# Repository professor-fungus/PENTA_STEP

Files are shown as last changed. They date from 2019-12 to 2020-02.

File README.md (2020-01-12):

# PENTA_STEP

I hate tracking down EMI through jumpers.

This is my attempt to create a stepper driver board that can be loaded with up to 5 stepper drives.

If one fails, it will require soldering rework; this may not be optimal for those without SMD rework tools.

The drives utilize Trinamic TMC5160's, based on the schematic for the TMC5160-BOB.

Why five drives? 
* 3 axes and 2 extruders for 3D printing.
* 3 cartesian axes and 2 orthogonal axes for milling.
* 5 axis robots.
* Too little space for 4 drives on a 100mmx100mm board from JLCPCB, so go big or go home.

If less than 5 axes are desired, less can be populated (although this wouldn't save much).

Target is a 4-layer board currently.

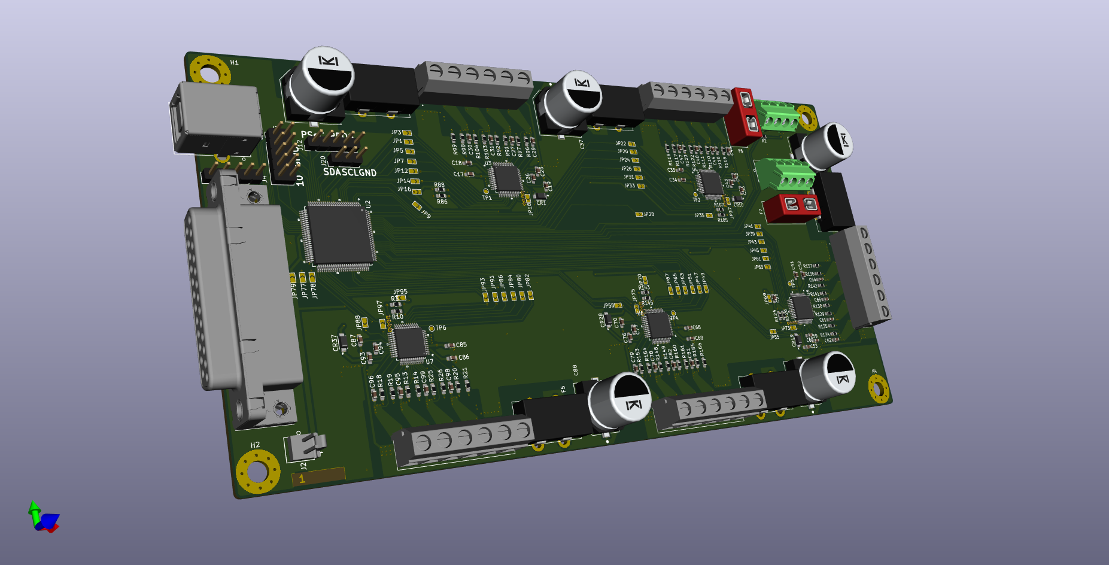
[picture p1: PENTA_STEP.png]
Test Image 1


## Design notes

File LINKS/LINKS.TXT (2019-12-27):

Dual MOSFET footprint info:
https://assets.nexperia.com/documents/outline-drawing/SOT1205.pdf

minimal ATTINY841
http://elecrab.com/archives/826

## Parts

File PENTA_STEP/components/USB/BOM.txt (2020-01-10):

3DX_CUI_DEVICES_Supplier: CUI Devices
3DX_CUI_DEVICES_Description: 3 µin Plating Thickness, White Insulator, USB Receptacle
3DX_CUI_DEVICES_Model Number: UJ2-BH-W1-TH

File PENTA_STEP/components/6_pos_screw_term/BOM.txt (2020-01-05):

3DX_CUI_DEVICES_Supplier: CUI Devices
3DX_CUI_DEVICES_Part Number: TB002-500-06BE
3DX_CUI_DEVICES_Description: 2~24 Poles, Screw Type, Horizontal, 5.0 Pitch, 22-12 (AWG), Terminal Block Connector

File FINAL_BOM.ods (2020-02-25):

REFDES |  |  |  |  | DPN |  | QTY
> C8-C11, C13-C16, C23-C25, C33, C40-C42, C50, C57-C59, C67, C74-C76, C84, C91-C93 | 100n | Capacitor_SMD:C_0603_1608Metric_Pad1.05x0.95mm_HandSolder |  | CL10B104KC8NNNC,1276-6807-1-ND | 478-10047-1-ND | 06031C104KAT2A | 27
> C3, C4, C6, C12 | 1u | Capacitor_SMD:C_0603_1608Metric_Pad1.05x0.95mm_HandSolder |  | CC0603KRX7R7BB105,311-1446-1-ND | 1276-6524-1-ND | CL10B105MO8NNWC | 4
> C17, C18, C34, C35, C51, C52, C68, C69, C85, C86 | 2u2 | Capacitor_SMD:C_0603_1608Metric_Pad1.05x0.95mm_HandSolder | ~ | EMK107BJ225KA-T,587-1430-1-ND | 1276-1040-1-ND | CL10A225KO8NNNC | 10
> C19, C29, C32, C36, C46, C49, C53, C63, C66, C70, C80, C83, C87, C97, C100 | 470n | Capacitor_SMD:C_0603_1608Metric_Pad1.05x0.95mm_HandSolder | ~ | CL10A474KP8NNNC,1276-1898-1-ND | 732-7905-1-ND | 885012106008 | 15
> C20, C37, C54, C71, C88 | 150u 80V | CUSTOM_FP:CAPAE1350X1400N_EEVFK1J151Q | ~ | EMHS800ARA181MKE0S,565-5083-1-ND | PCE3494CT-ND | EEV-FK1K151Q | 5
> C21, C22, C38, C39, C55, C56, C72, C73, C89, C90 | 10u | Capacitor_SMD:C_1210_3225Metric_Pad1.42x2.65mm_HandSolder |  | C3225X7R1N106K250AC,445-C3225X7R1N106K250ACCT-ND | 445-C3225X7R1N106M250ACCT-ND | C3225X7R1N106M250AC | 10
> C26, C43, C60, C77, C94 | 22n | Capacitor_SMD:C_0603_1608Metric_Pad1.05x0.95mm_HandSolder |  | C0603C223K1RACTU,399-3476-1-ND | 1276-1104-1-ND | CL10B223KB8NNNC | 5
> C27, C28, C30, C31, C44, C45, C47, C48, C61, C62, C64, C65, C78, C79, C81, C82, C95, C96, C98, C99 | 220n | Capacitor_SMD:C_0603_1608Metric_Pad1.05x0.95mm_HandSolder | ~ | CC0603ZRY5V9BB224,311-1830-1-ND | 1276-2367-1-ND | CL10F224ZB8NNNC | 20
> CR1, CR10, CR19, CR28, CR37 | PMEG6010CEGWX | CUSTOM_FP:PMEG6010CEGWX |  |  | S310FACT-ND | S310FA | 5
> F1-F5 | BLADE_Fuse | CUSTOM_FP:keystone_3549_2_fuseholder_THT | ~ |  | 36-3549-2-ND | 3549-2 | 5
> F6, F7 | BLADE_Fuse | CUSTOM_FP:keystone_3568_10_fuseholder_THT | ~ |  | 36-3568-10-ND | 3568-10 | 2
> H1-H4 | MountingHole_Pad | MountingHole:MountingHole_4.5mm_Pad_Via | ~ |  |  |  | 4
J1 | DB25_Female_LCNC | CUSTOM_FP:DSUB-25_Female_Horizontal_P2.77x2.84mm_EdgePinOffset7.70mm_Housed_MountingHolesOffset9.12mm | ~ |  | 2057-DB25-SL-25-ND | DB25-SL-25 | 1
J2 | MTA-100 | CUSTOM_FP:640456-2 | ~ |  | A1921-ND | 640456-2 | 1
J3 | USB_B | CUSTOM_FP:CUI_UJ2-BH-W1-TH | ~ |  | 102-5887-ND | UJ2-BH-W1-TH | 1
J4 | SPARE_IN | Connector_PinHeader_2.54mm:PinHeader_1x05_P2.54mm_Vertical | ~ |  |  |  | 1
J7 | CYP_GPIO | Connector_PinHeader_2.54mm:PinHeader_2x05_P2.54mm_Vertical | ~ |  |  |  | 1
> J5, J10, J11, J16, J17 | ENC_HEADER | Connector_PinHeader_1.00mm:PinHeader_1x04_P1.00mm_Vertical | ~ |  | HDR100MET40M-G-RA-TH-ND | HDR100MET40M-G-RA-TH | 5
J12 | PSoC_PROG | Connector_PinHeader_2.54mm:PinHeader_1x05_P2.54mm_Vertical | ~ |  |  |  | 1
J13 | PWR_SW_CH1 | CUSTOM_FP:1776275-4 | ~ |  | 277-1781-ND | 1988972 | 1
> J9, J14, J15, J18, J19 | SCREW TERM | CUSTOM_FP:CUI_TB002-500-06BE | ~ |  | 102-6149-ND | TB002-500-06BE | 5
J20 | CYP_I2C | Connector_PinHeader_2.54mm:PinHeader_1x03_P2.54mm_Vertical | ~ |  |  |  | 1
J21 | PWR_SW_CH2 | CUSTOM_FP:1776275-4 | ~ |  | 277-1781-ND | 1988972 | 1
> JP1, JP3, JP5, JP7, JP9, JP11-JP16, JP18-JP20, JP22, JP24, JP26, JP28, JP30-JP35, JP37-JP39, JP41, JP43, JP45, JP47, JP49, JP51, JP53, JP55, JP57, JP58, JP60-JP70, JP73-JP80, JP82, JP84, JP86, JP88, JP90-JP95, JP97, JP98 | SolderJumper_2_Open | CUSTOM_FP:small_triangle_jumper | ~ |  |  |  | 68
> Q1-Q20 | BUK9K45-100E,115 | CUSTOM_FP:TRANS_BUK7K12-60EX | https://assets.nexperia.com/documents/data-sheet/BUK9K45-100E.pdf |  | 1727-7272-1-ND | BUK9K45-100E,115 | 20
> Q2, Q4, Q6, Q8, Q10, Q12, Q14, Q16, Q18, Q20 | BUK9K45-100E,115 | CUSTOM:TRANS_BUK7K12-60EX | https://assets.nexperia.com/documents/data-sheet/BUK9K45-100E.pdf |  | 1727-7272-1-ND | BUK9K45-100E,115 | 10
Q21 | AON7804 | CUSTOM_FP:DFN3X3_AON7804 |  |  | 785-1586-1-ND | AON7804 | 1
> R1, R2, R12, R90, R109, R128, R147 | 2R2 | Resistor_SMD:R_0603_1608Metric_Pad1.05x0.95mm_HandSolder | ~ | RMCF0603FT2R20,RMCF0603FT2R20CT-ND | 311-2.2HRCT-ND | RC0603FR-072R2L | 7
> R5, R6, R13, R14, R18-R21, R25, R26, R91, R92, R96-R99, R103, R104, R110, R111, R115-R118, R122, R123, R129, R130, R134-R137, R141, R142, R148, R149, R153-R156, R160, R161 | 22R | Resistor_SMD:R_0603_1608Metric_Pad1.05x0.95mm_HandSolder | ~ | CRGCQ0603J22R,A130081CT-ND | P22.0HCT-ND | ERJ-3EKF22R0V | 42
> R4, R10, R87, R88, R106, R107, R125, R126, R144, R145 | DNP | Resistor_SMD:R_0603_1608Metric_Pad1.05x0.95mm_HandSolder | ~ | ERJ-3GEY0R00V,P0.0GCT-ND | 311-0.0GRCT-ND | RC0603JR-070RL | 10
> R3, R11, R86, R89, R105, R108, R124, R127, R143, R146 | 0R | Resistor_SMD:R_0603_1608Metric_Pad1.05x0.95mm_HandSolder | ~ | ERJ-3GEY0R00V,P0.0GCT-ND | 311-0.0GRCT-ND | RC0603JR-070RL | 10
> R15, R16, R22, R23, R93, R94, R100, R101, R112, R113, R119, R120, R131, R132, R138, R139, R150, R151, R157, R158 | 47R | Resistor_SMD:R_0603_1608Metric_Pad1.05x0.95mm_HandSolder | ~ | RMCF0603FT47R0,RMCF0603FT47R0CT-ND | A129672CT-ND | CRGCQ0603F47R | 20
> R17, R24, R95, R102, R114, R121, R133, R140, R152, R159 | 0R022 | CUSTOM_FP:WSH2818R0500FEA | ~ |  | 541-10297-1-ND | WSHM2818R0220FEA | 10
> R162, R163 | 10k | Resistor_SMD:R_0603_1608Metric_Pad1.05x0.95mm_HandSolder | ~ | ERJ-3GEYJ103V,P10KGCT-ND | 311-10KGRCT-ND | RC0603JR-0710KL | 2
> TP1-TP4, TP6 | CLK16 | TestPoint:TestPoint_Pad_D1.0mm | ~ |  |  |  | 5
TP5 | PAR_SPARE | TestPoint:TestPoint_Pad_D1.0mm | ~ |  |  |  | 1
U2 | CY8C5468AXI-LP106 | CUSTOM_FP:CY8C5468AXI-LP106 |  |  | 2015-CY8C5468AXI-LP106-ND | CY8C5468AXI-LP106 | 1
> U3-U7 | TMC5160-TA | CUSTOM_FP:TMC5160-TA |  |  | 1460-1249-ND | TMC5160-TA | 5

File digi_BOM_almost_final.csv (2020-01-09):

Index | Quantity | Part Number | Manufacturer Part Number | Description | Customer Reference | Available | Backorder | Unit Price | Extended Price USD
1 | 1 | ATTINY841-SSU-ND | ATTINY841-SSU | IC MCU 8BIT 8KB FLASH 14SOIC | U1 | 1 | 0 | 1.01000 | 1.01
2 | 1 | 102-5887-ND | UJ2-BH-W1-TH | CONN RCPT USB2.0 TYPEB 4POS R/A | J3 | 1 | 0 | 0.54000 | 0.54
3 | 2 | 102-6149-ND | TB002-500-06BE | TERMINAL BLOCK, SCREW TYPE, 5.00 | J14 | 2 | 0 | 0.95000 | 1.90
4 | 16 | 1276-2367-1-ND | CL10F224ZB8NNNC | CAP CER 0.22UF 50V Y5V 0603 | C27 | 16 | 0 | 0.07900 | 1.26
5 | 4 | 1460-1249-ND | TMC5160-TA | IC MTR DRVR BIPOLAR 8-60V 48TQFP | U3 | 4 | 0 | 5.61000 | 22.44
6 | 16 | 1727-7272-1-ND | BUK9K45-100E,115 | MOSFET 2N-CH 100V 21A LFPAK56D | Q9 | 16 | 0 | 0.96000 | 15.36
7 | 1 | 2015-CY8C5468AXI-LP106-ND | CY8C5468AXI-LP106 | NO WARRANTY | U2 | 1 | 0 | 2.23000 | 2.23
8 | 1 | 2057-DB25-SL-25-ND | DB25-SL-25 | D-SUB R/A 25 WAY SOCKET | J1 | 1 | 0 | 1.42000 | 1.42
9 | 1 | 277-1667-ND | 1935161 | TERM BLK 2POS SIDE ENTRY 5MM PCB | J2 | 1 | 0 | 0.43000 | 0.43
10 | 1 | 311-10KGRCT-ND | RC0603JR-0710KL | RES SMD 10K OHM 5% 1/10W 0603 | R5 | 1 | 0 | 0.10000 | 0.10
11 | 4 | 311-2.2HRCT-ND | RC0603FR-072R2L | RES SMD 2.2 OHM 1% 1/10W 0603 | R90 | 4 | 0 | 0.10000 | 0.40
12 | 24 | 478-10047-1-ND | 06031C104KAT2A | CAP CER .1UF 100V X7R 0603 | C2 | 24 | 0 | 0.11600 | 2.78
13 | 1 | 587-5869-1-ND | JMK107ABJ106MA-T | CAP CER 10UF 6.3V X5R 0603 | C1 | 1 | 0 | 0.13000 | 0.13
14 | 2 | 587-5869-1-ND | JMK107ABJ106MA-T | CAP CER 10UF 6.3V X5R 0603 | C7 | 2 | 0 | 0.13000 | 0.26
15 | 1 | 631-1011-1-ND | FC4SDCBMF10.0-T1 | CRYSTAL 10.0000MHZ 20PF SMD | Y1 | 1 | 0 | 0.32000 | 0.32
16 | 12 | 732-7905-1-ND | 885012106008 | CAP CER 0.47UF 10V X5R 0603 | C19 | 12 | 0 | 0.06900 | 0.83
17 | 16 | A129672CT-ND | CRGCQ0603F47R | CRGCQ 0603 47R 1% | R93 | 16 | 0 | 0.03000 | 0.48
18 | 32 | P22.0HCT-ND | ERJ-3EKF22R0V | RES SMD 22 OHM 1% 1/10W 0603 | R92 | 32 | 0 | 0.05700 | 1.82
19 | 4 | PCE3494CT-ND | EEV-FK1K151Q | CAP ALUM 150UF 20% 80V SMD | C20 | 4 | 0 | 1.32000 | 5.28
20 | 10 | 1276-1040-1-ND | CL10A225KO8NNNC | CAP CER 2.2UF 16V X5R 0603 | C17 | 10 | 0 | 0.08500 | 0.85
21 | 10 | 1276-1104-1-ND | CL10B223KB8NNNC | CAP CER 0.022UF 50V X7R 0603 | C26 | 10 | 0 | 0.04200 | 0.42
22 | 10 | 1276-6524-1-ND | CL10B105MO8NNWC | CAP CER 1UF 16V X7R 0603 | C12 | 10 | 0 | 0.04200 | 0.42
23 | 100 | 311-0.0GRCT-ND | RC0603JR-070RL | RES SMD 0 OHM JUMPER 1/10W 0603 | R41 | 100 | 0 | 0.00770 | 0.77
24 | 10 | 311-10KGRCT-ND | RC0603JR-0710KL | RES SMD 10K OHM 5% 1/10W 0603 | R162 | 10 | 0 | 0.01900 | 0.19
25 | 10 | 445-C3225X7R1N106M250ACCT-ND | C3225X7R1N106M250AC | COMMERCIAL GRADE GENERAL PURPOSE | C21 | 10 | 0 | 0.83500 | 8.35
26 | 8 | 541-10297-1-ND | WSHM2818R0220FEA | RES 0.022 OHM 1% 7W 2818 | R95 | 8 | 0 | 1.41000 | 11.28

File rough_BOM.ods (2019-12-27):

Index | Quantity | Part Number | Manufacturer Part Number | Description | Customer Reference | Available | Backorder | Unit Price | Extended Price USD
1 | 16 | 478-10047-1-ND | 06031C104KAT2A | CAP CER .1UF 100V X7R 0603 | C1,C5,C7,C8 | 16 | 0 | 0.116 | 1.86
2 | 16 | 1276-6807-1-ND | CL10B104KC8NNNC | CAP CER 0.1UF 100V X7R 0603 | C1,C5,C7,C8 | 16 | 0 | 0.107 | 1.71
3 | 8 | 1276-1040-1-ND | CL10A225KO8NNNC | CAP CER 2.2UF 16V X5R 0603 | C2,C3 | 8 | 0 | 0.12 | 0.96
4 | 8 | 587-1430-1-ND | EMK107BJ225KA-T | CAP CER 2.2UF 16V X5R 0603 | C2,C3 | 8 | 0 | 0.12 | 0.96
5 | 4 | 732-7905-1-ND | 885012106008 | CAP CER 0.47UF 10V X5R 0603 | C4 | 4 | 0 | 0.1 | 0.40
6 | 4 | 1276-1898-1-ND | CL10A474KP8NNNC | CAP CER 0.47UF 10V X5R 0603 | C4 | 4 | 0 | 0.11 | 0.44
7 | 4 | 1276-1104-1-ND | CL10B223KB8NNNC | CAP CER 0.022UF 50V X7R 0603 | C6 | 4 | 0 | 0.1 | 0.40
8 | 4 | 399-3476-1-ND | C0603C223K1RACTU | CAP CER 0.022UF 100V X7R 0603 | C6 | 4 | 0 | 0.1 | 0.40
9 | 8 | 1276-1248-1-ND | CL21A475KBQNNNE | CAP CER 4.7UF 50V X5R 0805 | C9,C10 | 8 | 0 | 0.39 | 3.12
10 | 8 | 490-10751-1-ND | GRM21BR61H475KE51L | CAP CER 4.7UF 50V X5R 0805 | C9,C10 | 8 | 0 | 0.37 | 2.96
11 | 16 | 311-1830-1-ND | CC0603ZRY5V9BB224 | CAP CER 0.22UF 50V Y5V 0603 | C11,C12,C13,C14 | 16 | 0 | 0.086 | 1.38
12 | 16 | 1276-2367-1-ND | CL10F224ZB8NNNC | CAP CER 0.22UF 50V Y5V 0603 | C11,C12,C13,C14 | 16 | 0 | 0.079 | 1.26
13 | 8 | 587-3171-1-ND | UMK107ABJ474KA-T | CAP CER 0.47UF 50V X5R 0603 | C15,C16 | 8 | 0 | 0.19 | 1.52
14 | 8 | 1276-2377-1-ND | CL10F474ZB8NNNC | CAP CER 0.47UF 50V Y5V 0603 | C15,C16 | 8 | 0 | 0.13 | 1.04
15 | 4 | 1830-1061-1-ND | IN-S63AT5B | LED BLUE CLEAR 0603 SMD | D1 | 4 | 0 | 0.34 | 1.36
16 | 4 | 732-4966-1-ND | 150060BS75000 | LED BLUE CLEAR 0603 SMD | D1 | 4 | 0 | 0.16 | 0.64
17 | 4 | 1460-1249-ND | TMC5160-TA | IC MTR DRVR BIPOLAR 8-60V 48TQFP | IC1 | 4 | 0 | 5.61 | 22.44
18 | 4 | P0.0GCT-ND | ERJ-3GEY0R00V | RES SMD 0 OHM JUMPER 1/10W 0603 | R2 | 4 | 0 | 0.1 | 0.40
19 | 4 | 311-0.0GRCT-ND | RC0603JR-070RL | RES SMD 0 OHM JUMPER 1/10W 0603 | R2 | 4 | 0 | 0.1 | 0.40
20 | 32 | P22.0HCT-ND | ERJ-3EKF22R0V | RES SMD 22 OHM 1% 1/10W 0603 | R3, R4, R5, R6, R13, R14, R15, R16 | 32 | 0 | 0.057 | 1.82
21 | 32 | A130081CT-ND | CRGCQ0603J22R | CRGCQ 0603 22R 5% | R3, R4, R5, R6, R13, R14, R15, R16 | 32 | 0 | 0.021 | 0.67
22 | 16 | RMCF0603FT47R0CT-ND | RMCF0603FT47R0 | RES 47 OHM 1% 1/10W 0603 | R7, R8, R9, R10 | 16 | 0 | 0.016 | 0.26
23 | 16 | A129672CT-ND | CRGCQ0603F47R | CRGCQ 0603 47R 1% | R7, R8, R9, R10 | 16 | 0 | 0.03 | 0.48
24 | 8 | 541-10297-1-ND | WSHM2818R0220FEA | RES 0.022 OHM 1% 7W 2818 | R11,R12 |  |  | 1.41 | 11.28
25 | 4 | 311-2.2HRCT-ND | RC0603FR-072R2L | RES SMD 2.2 OHM 1% 1/10W 0603 | R17 | 4 | 0 | 0.1 | 0.40
26 | 4 | RMCF0603FT2R20CT-ND | RMCF0603FT2R20 | RES 2.2 OHM 1% 1/10W 0603 | R17 | 4 | 0 | 0.1 | 0.40
27 | 4 | 311-1.00KHRCT-ND | RC0603FR-071KL | RES SMD 1K OHM 1% 1/10W 0603 | R18 | 4 | 0 | 0.1 | 0.40
28 | 4 | RMCF0603FT1K00CT-ND | RMCF0603FT1K00 | RES 1K OHM 1% 1/10W 0603 | R18 | 4 | 0 | 0.1 | 0.40
29 | 16 | 1727-7272-1-ND | BUK9K45-100E,115 | MOSFET 2N-CH 100V 21A LFPAK56D | Q1,Q2,Q3,Q4 |  |  | 0.96 | 15.36
 |  |  |  |  |  |  |  |  |  | Board T: | 63.36
 |  | 0.022
 |  | 15
 |  | 4.95

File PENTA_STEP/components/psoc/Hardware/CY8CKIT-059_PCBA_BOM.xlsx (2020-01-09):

TITLE |  | CY8CKIT-059 PSoC 5LP Prototyping Kit
PCA # |  | 121-60210-01 |  | REV | 06
SCH # |  | 630-60242-01
DATE |  | 2018-01-16
Item | Qty | Cy_Part# | Reference | Value | Description | Mfr Name | Mfr Part Number
1 | 1 | 600-60243-01 | N/A | N/A | PCB, 108.89mm x 24.13mm, High Tg, ENIG finish, 2 layer, Color = BLACK, Silk = WHITE | Cypress Semiconductors | 600-60178-01
2 | 19 | 510-60026-01 | C1,C3,C5,C6,C10,C11,C14, C18,C20,C22,C23,C27,C29, C32,C33,C34,C35,C39,C40 | 0.1 uF | CAP .1UF 16V CERAMIC Y5V 0402 | AVX Corporation | 0402YG104ZAT2A
3 | 1 | 510-60190-01 | C4 | 2200 pF | CAP CER 2200PF 50V 5% NP0 0805 | Murata Electronics | GRM2165C1H222JA01D
4 | 17 | 510-60088-01 | C7,C8,C9,C12,C13,C15,C16, C21,C24,C25,C26,C28,C30, C31,C36,C37,C38 | 1.0 uF | CAP CERAMIC 1.0UF 25V X5R 0603 10% | Taiyo Yuden | TMK107BJ105KA-T
5 | 1 | 510-60214-01 | C19 | 0.01 uF | CAP 10000PF 16V CERAMIC 0402 SMD | TDK Corporation | C1005X7R1C103K050BA
6 | 2 | 510-60318-01 | C41,C42 | 22 pF | CAP CER 22PF 50V 2% C0G 0402 | TDK Corporation | C1005C0G1H220G050BA
7 | 2 | 530-60015-01 | D1,D2 | MBR0520L | DIODE , SCHOTTKY, 20V, 0.5A, 400mW, SOD-123 | Fairchild Semiconductor | MBR0520L
8 | 2 | 760-60010-01 | F1,F2 | PTC Resettable Fuse | FUSE, PTC Resettable, 0.50A, 16V, 1210, SMD | Bel Fuse Inc | 0ZCH0050FF2G
9 | 1 | 720-60132-01 | J6 | USB Micro-B | CONN RCPT STD MICRO USB TYPE B | FCI | 10103594-0001LF
10 | 1 | 534-60040-01 | LED1 | User LED BLUE | LED, BLUE, CLEAR, 0805, SMD | Lite-On Inc | LTST-C170TBKT
11 | 1 | 534-60022-01 | LED2 | POWER LED Amber | LED 595NM AMB DIFF 0805 SMD | Avago Technologies US Inc. | HSMA-C170
12 | 1 | 534-60024-01 | LED3 | Status LED Green | LED GREEN CLEAR 0805 SMD | Chicago Miniature/Visual Communications Company-VCC | CMD17-21VGC/TR8
13 | 2 | 500-60445-01 | R2,R3 | 15K | RES SMD 15K OHM 5% 1/10W 0402 | Panasonic - ECG | ERJ-2GEJ153X
14 | 4 | 500-60085-01 | R4,R6,R16,R17 | 22E | RES, 22 OHM, 1%, 100PPM, 1/16W, 0402 | Panasonic - ECG | ERJ-2RKF22R0X
15 | 3 | 500-60037-01 | R5,R22,R23 | ZERO | RES SMD 0.0 OHM JUMPER 06O3 1/10W | Panasonic - ECG | ERJ-3GEY0R00V
16 | 2 | 500-60216-01 | R7,R9 | 2.2K | RES 2.2K OHM 1/10W 5% 0603 SMD | Panasonic - ECG | ERJ-3GEYJ222V
17 | 1 | 500-60134-01 | R10 | 560 ohm | RES, 560 OHM, 5%, 200PPM, 1/10W, 0603, SMD | Panasonic-ECG | ERJ-3GEYJ561V
18 | 1 | 500-60075-01 | R12 | 100K | RES 100K OHM 1/10W 5% 0402 SMD | Panasonic - ECG | ERJ-2GEJ104X
19 | 2 | 500-60446-01 | R13,R14 | 30K | RES SMD 30K OHM 5% 1/10W 0402 | Panasonic - ECG | ERJ-2GEJ303X
20 | 4 | 500-60215-01 | R8,R11,R15,R20 | ZERO | RES SMD 0.0 OHM JUMPER 1/8W 0805 | Panasonic - ECG | ERJ-6GEY0R00V
21 | 2 | 500-60390-01 | R18,R21 | 820 ohm | RES, 820 OHM, 5%, 1/10W, 0603 | Panasonic - ECG | ERJ-3GEYJ821V
22 | 2 | 770-60025-01 | SW1,SW3 | Switch | SW, TACTILE SWITCH, SPST-NO, 0.05A, 32V | C&K Components | KMR221GLFS
23 | 1 | 530-60012-01 | TVS1 | TVS DIODE | DIODE, TVS, 5V, 350W, SOD-323 | Semtech | SD05.TCT
24 | 1 | CY8C5868LTI-LP039 | U1 | CY8C5868LTI-LP039 QFN68 | PSoC 5LP CYC58LP, 67 MHz | Cypress Semiconductor | CY8C5868LTI-LP039
25 | 1 | CY8C5888LTI-LP097 | U2 | CY8C5888LTI-LP097 QFN68 | PSoC 5LP CYC58LP, 80 MHz | Cypress Semiconductor | CY8C5888LTI-LP097
26 | 1 | 532-60001-01 | U3 | NTZD3152P | FET DUAL P-CH 20V 430mA SOT-563 | ON Semiconductor | NTZD3152PT1G
No Load Components
1 | 2 | 510-60026-01 | C2,C17 | 0.1 uF | CAP .1UF 16V CERAMIC Y5V 0402 | AVX Corporation | 0402YG104ZAT2A
2 | 2 | xxx-xxxxxx | J1,J2 | HDR 1x26 | CONN HDR BRKWAY 26POS VERT 2.54mm,15AU, TH | TE Connectivity | 2-104427-4
3 | 2 | 710-60020-01 | J3,J7 | HDR 1x5 | CONN HEADER 5POS .100 VERT TIN | Molex | 22-23-2051
4 | 1 | 720-60028-01 | J4 | HDR 1x2 | CONN HEADR BRKWAY .100 02POS STR | TE Connectivity | 9-146280-0-02
5 | 1 | 710-60030-01 | J5 | 50MIL KEYED SMD | CONN, HEADER, MALE, 1.27mm, 10POS, GOLD, SMD | Samtec Inc | FTSH-105-01-L-DV-K
6 | 2 | xxx-xxxxx | J8,J9 | HDR 1x7 | CONN HEADER FEMALE 7POS .1" GOLD | Sullins Connector Solutions | PPPC071LFBN-RC
7 | 2 | 500-60360-01 | R1,R19 | 4.7K | RES SMD 4.7K OHM 5% 1/10W 0402 | Panasonic - ECG | ERJ-2GEJ472X
8 | 1 | xxx-xxxx | SW2 | SW PUSHBUTTON | SWITCH TACTILE SPST-NO 0.05A 12V | C&K Components | PTS635SL50 LFS
9 | 3 | 711-60002-01 | TP1,TP2,TP3 | BLACK | TP, TEST POINT, 0.040"D, BLACK, TH | Keystone Electronics | 5000
10 | 1 | 542-60003-01 | Y1 | BLACK | CRYSTAL 32.768KHZ 12.5PF THRU | Citizen Finetech Miyota | CFS308-32.768KDZF-UB
Label
38 | 1 | N/A | N/A |  | LBL, PCA Label, Vendor Code, Datecode, Serial Number 121-60210-01 REV 01 (YYWWVVXXXXX) | Cypress Semiconductor
39 | 1 | N/A | N/A |  | LBL, PCBA Anti-Static Warning, 10mm X 10mm | Cypress Semiconductor

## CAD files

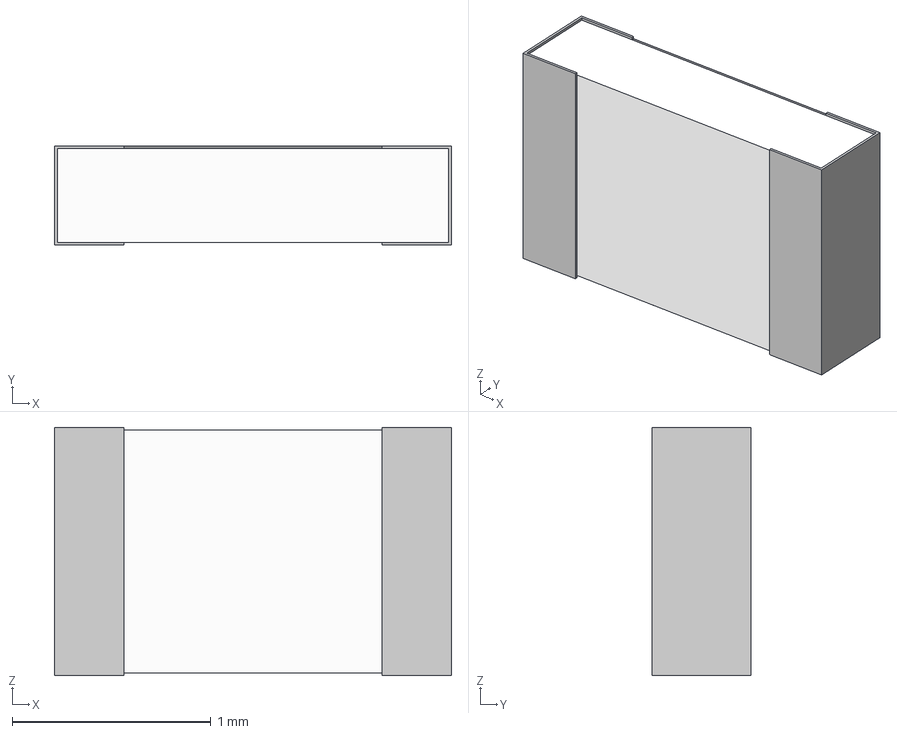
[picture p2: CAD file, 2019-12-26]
PENTA_STEP/components/0805R.stp
2.00 x 0.5 x 1.25 mm

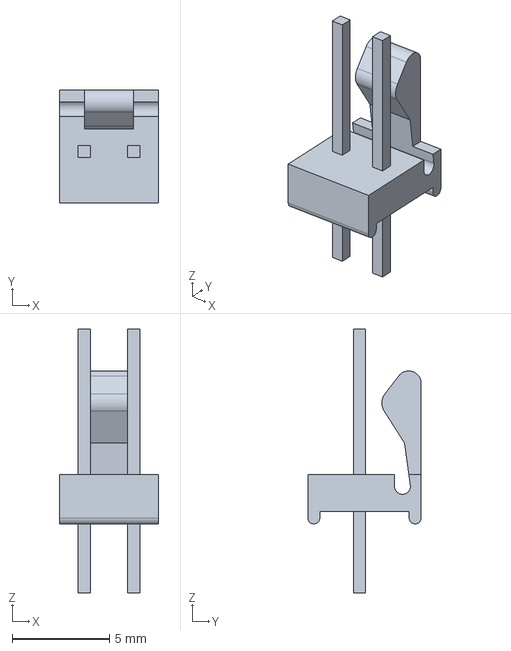
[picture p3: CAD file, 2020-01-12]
PENTA_STEP/components/2_pos_MTA100/c-640456-2-aa-3d.stp
5.08 x 5.84 x 13.6 mm

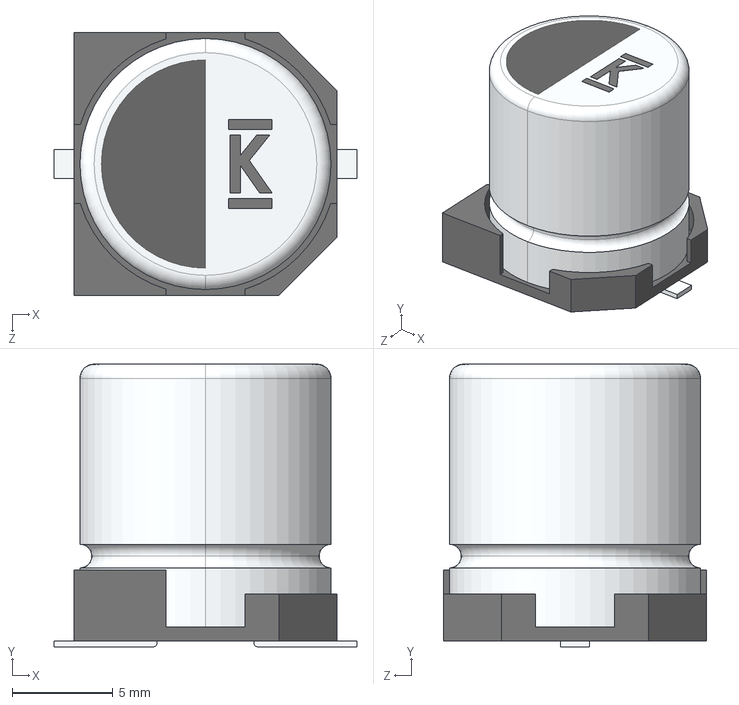
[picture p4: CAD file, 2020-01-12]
PENTA_STEP/components/electrol_cap/EDH108M016A9RAA.step
15.0 x 14.0 x 13.0 mm

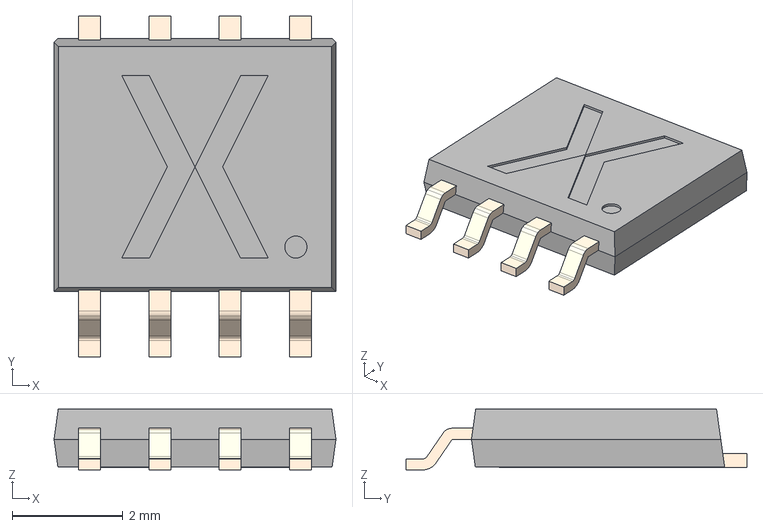
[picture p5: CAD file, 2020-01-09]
PENTA_STEP/components/FETs/SOT1205.step
5.10 x 6.16 x 1.10 mm

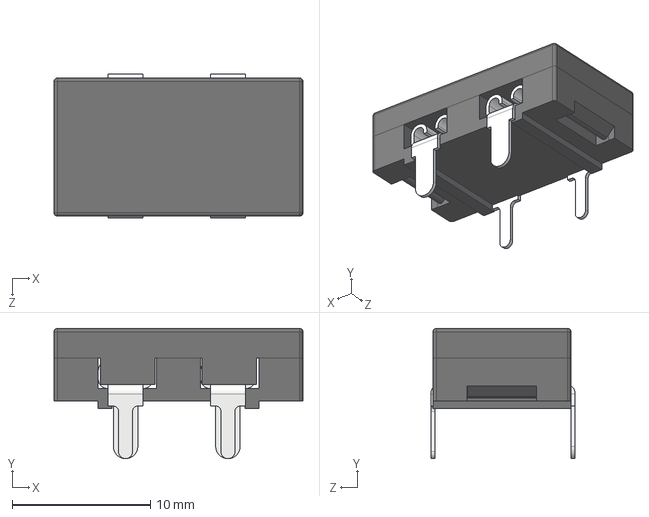
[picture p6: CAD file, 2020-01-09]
PENTA_STEP/components/fuse_holder/keystone-PN3549-2.STEP
18.0 x 9.44 x 10.5 mm

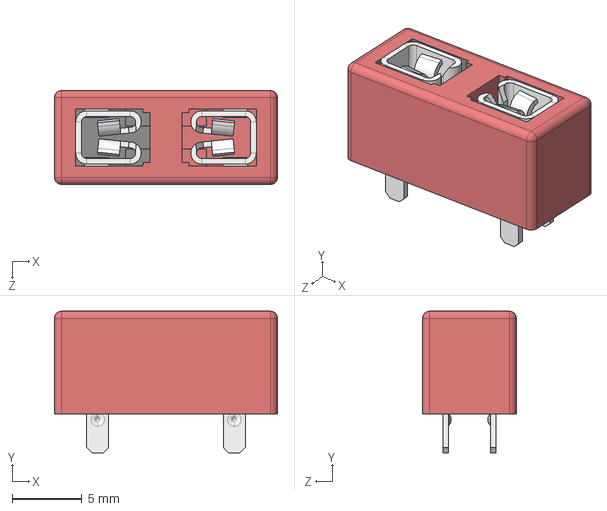
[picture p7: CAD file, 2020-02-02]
PENTA_STEP/components/fuse_holder_top_entry/keystone-PN3568-10_THT.STEP
16.0 x 10.2 x 6.73 mm

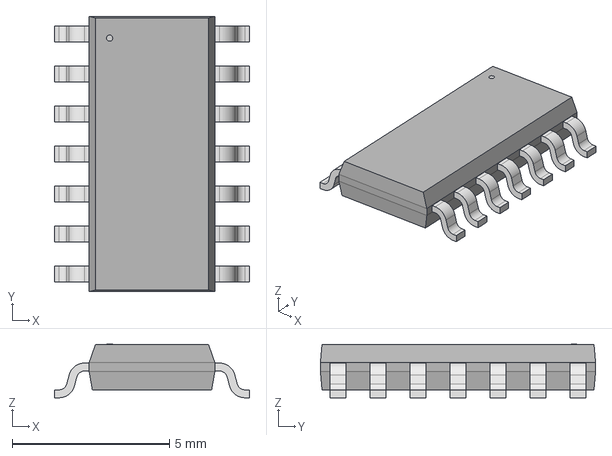
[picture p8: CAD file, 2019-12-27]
PENTA_STEP/components/MCU/2019-12-26_17-57-45/STEP/14S1.step
6.20 x 8.75 x 1.70 mm

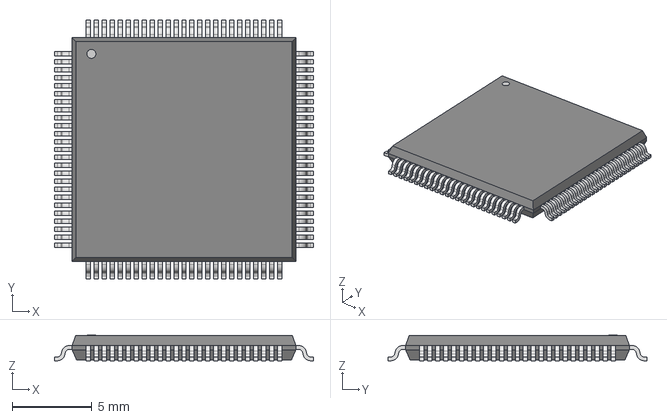
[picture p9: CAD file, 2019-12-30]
PENTA_STEP/components/psoc/2019-12-30_03-27-28/STEP/TQFP-100.step
16.3 x 16.3 x 1.60 mm

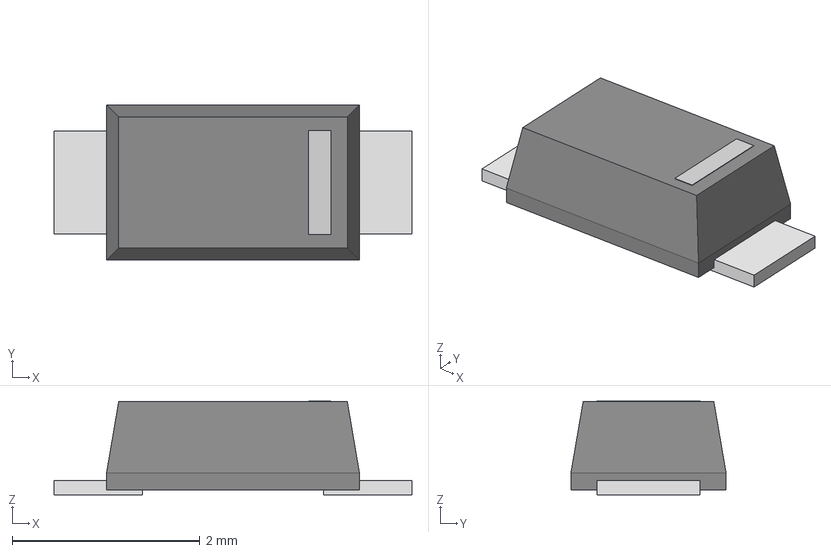
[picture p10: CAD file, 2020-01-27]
PENTA_STEP/components/rect_diode_bridge/2020-01-26_18-36-00/STEP/DIODE_SOD123LF_2P9X1P8-L.step
3.81 x 1.65 x 0.997 mm

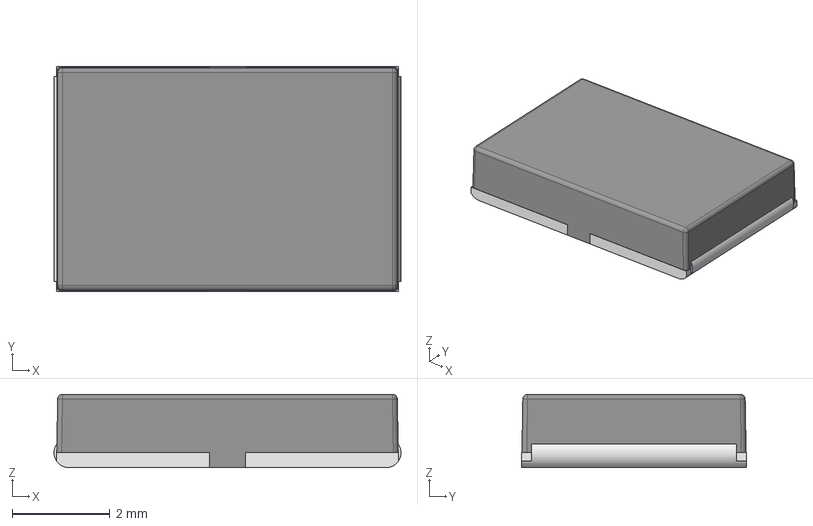
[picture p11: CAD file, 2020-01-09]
PENTA_STEP/components/sense_resist/WSHM2818.stp
7.10 x 4.60 x 1.50 mm

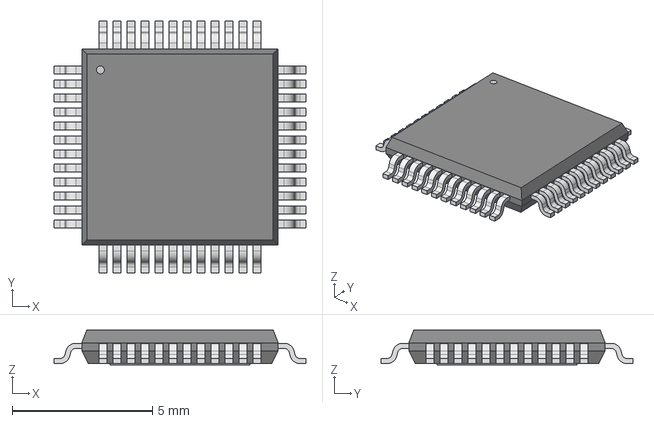
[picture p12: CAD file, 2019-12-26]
PENTA_STEP/components/TMC5160/2019-12-26_03-08-04/STEP/eTQFP48_9x9.step
8.99 x 8.99 x 1.25 mm

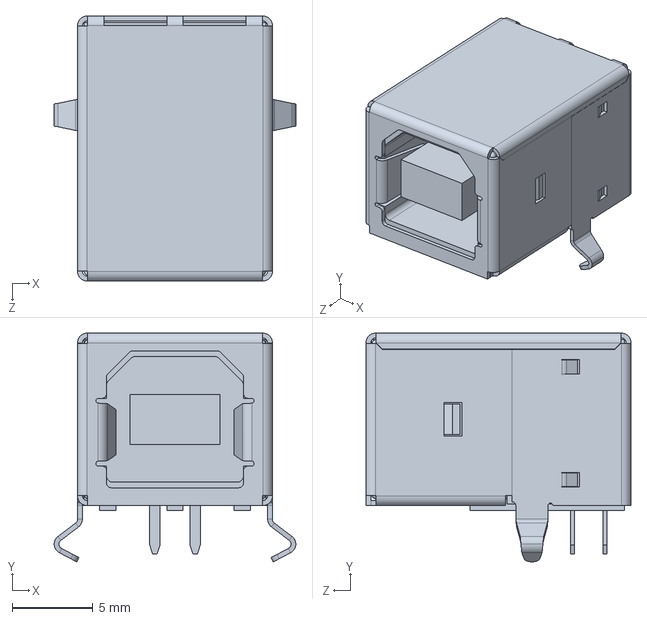
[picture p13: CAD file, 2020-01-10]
PENTA_STEP/components/USB/CUI_DEVICES_UJ2-BH-W1-TH.step
15.0 x 14.2 x 16.5 mm

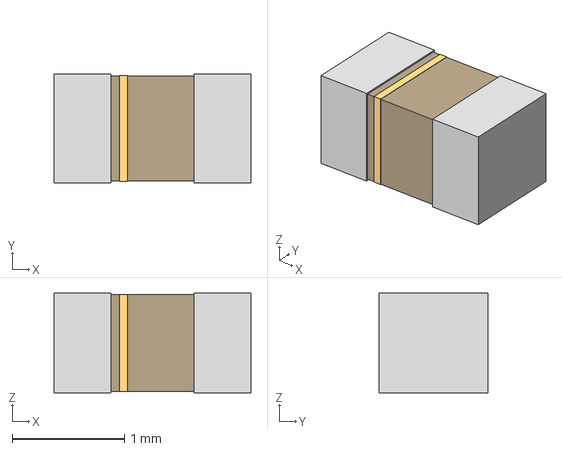
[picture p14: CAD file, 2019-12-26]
PENTA_STEP/components/0603C.step
1.75 x 0.966 x 0.889 mm

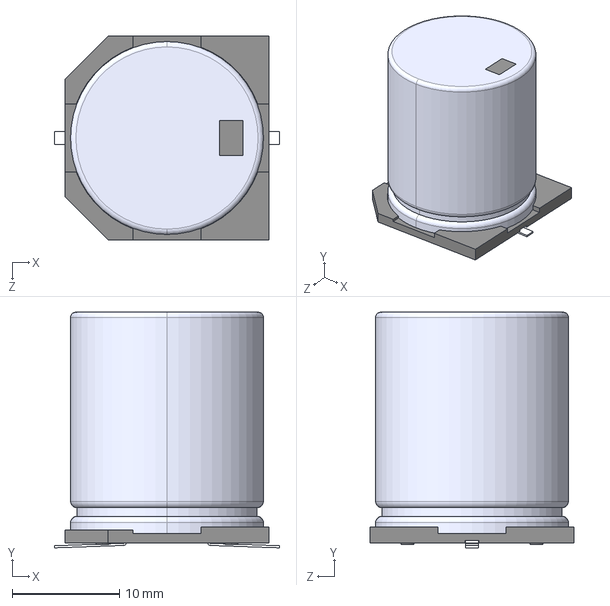
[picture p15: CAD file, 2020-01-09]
PENTA_STEP/components/electrol_cap/EEV-EB2D101M--3DModel-STEP-56544.STEP
21.0 x 22.0 x 19.0 mm

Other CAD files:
PENTA_STEP/components/MCU/2019-12-26_17-57-45/STEP/14S1-M.step
PENTA_STEP/components/psoc/2019-12-30_03-27-28/STEP/TQFP-100-M.step
PENTA_STEP/components/rect_diode_bridge/2020-01-26_18-36-00/STEP/DIODE_SOD123LF_2P9X1P8-M.step
PENTA_STEP/components/TMC5160/2019-12-26_03-08-04/STEP/eTQFP48_9x9-M.step
PENTA_STEP/components/01005R.stp
PENTA_STEP/components/0201R.stp
PENTA_STEP/components/0402R.stp
PENTA_STEP/components/0603R.stp
PENTA_STEP/components/0805C.step
PENTA_STEP/components/1206R.stp
PENTA_STEP/components/1210R.stp
PENTA_STEP/components/2010R.stp
PENTA_STEP/components/2512R.stp
PENTA_STEP/components/2_pos_screw_term/1935161--3DModel-STEP-56544.STEP
PENTA_STEP/components/4_pos_screw_term/pxc_1988972_01_PTA-1-5-4-3-5_3D.stp
PENTA_STEP/components/6_pos_screw_term/CUI_DEVICES_TB002-500-06BE.step
PENTA_STEP/components/MCU/2019-12-26_17-57-45/STEP/14S1-L.step
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

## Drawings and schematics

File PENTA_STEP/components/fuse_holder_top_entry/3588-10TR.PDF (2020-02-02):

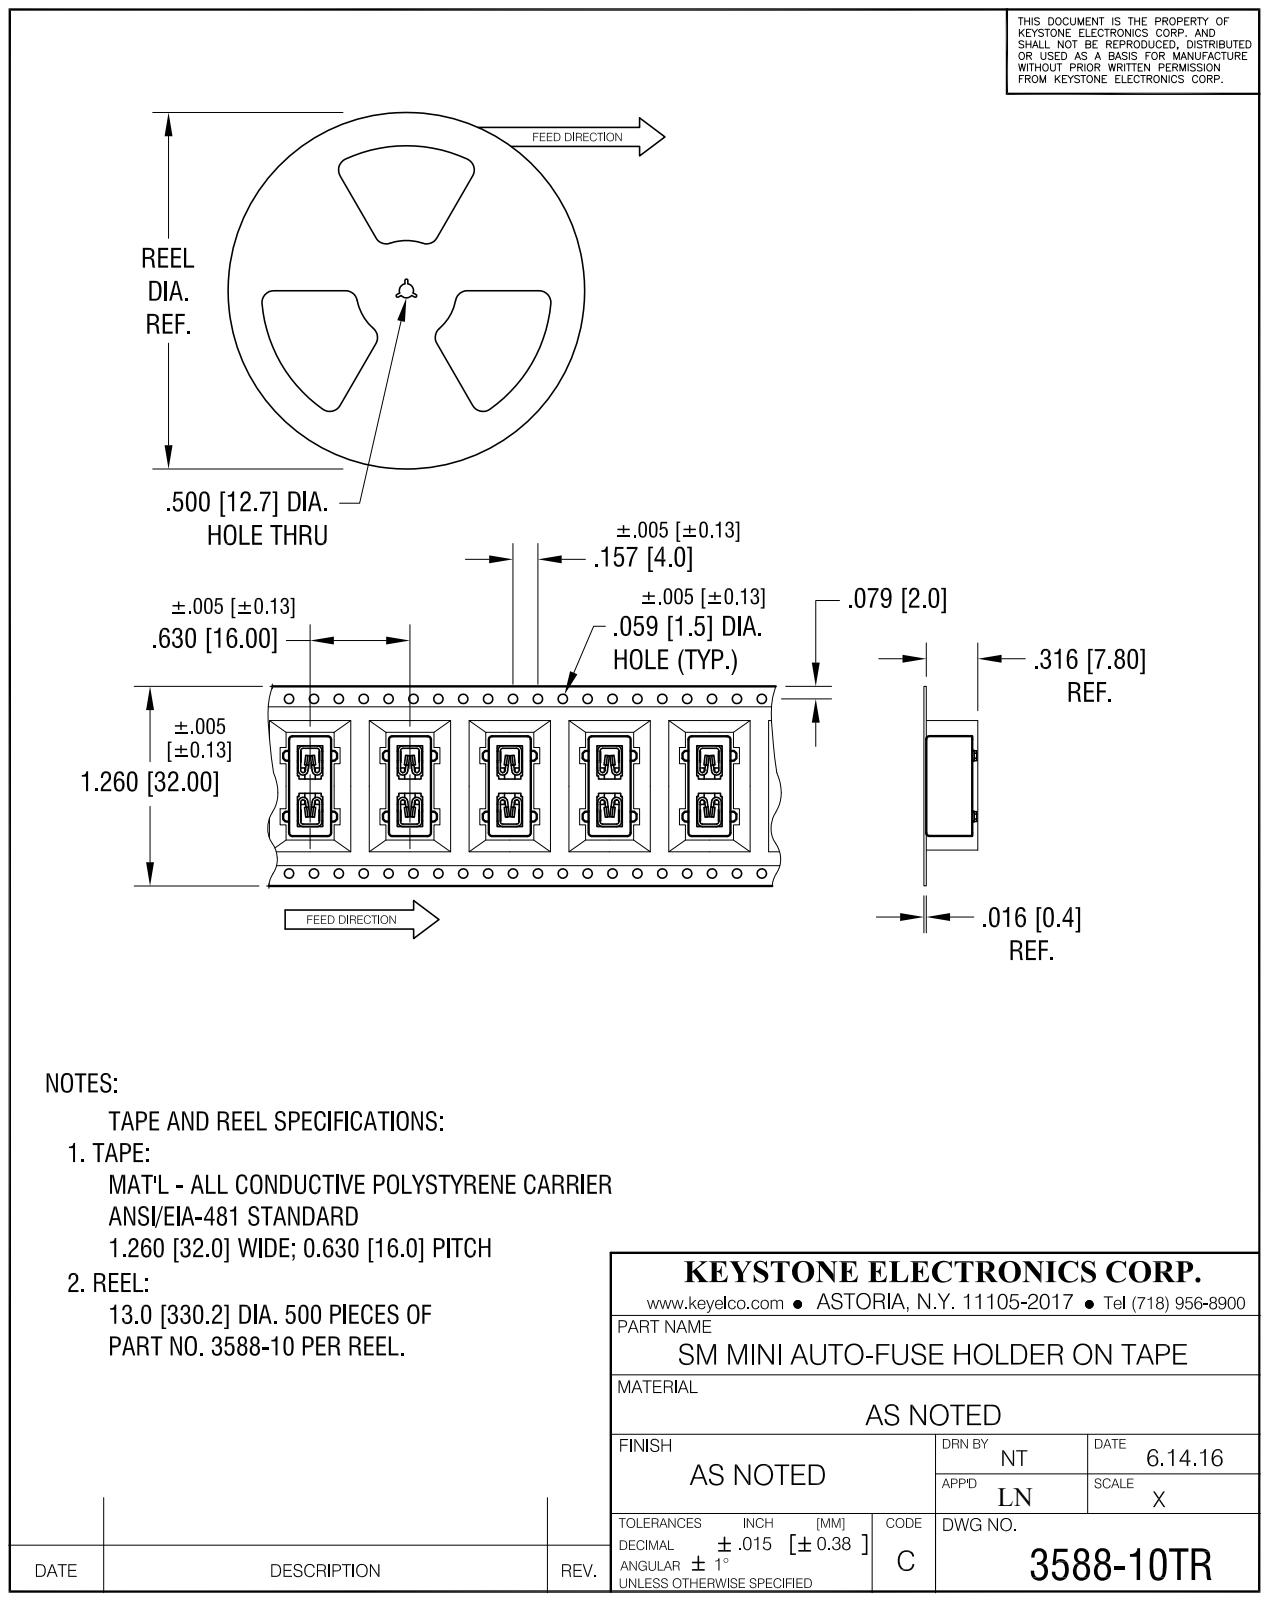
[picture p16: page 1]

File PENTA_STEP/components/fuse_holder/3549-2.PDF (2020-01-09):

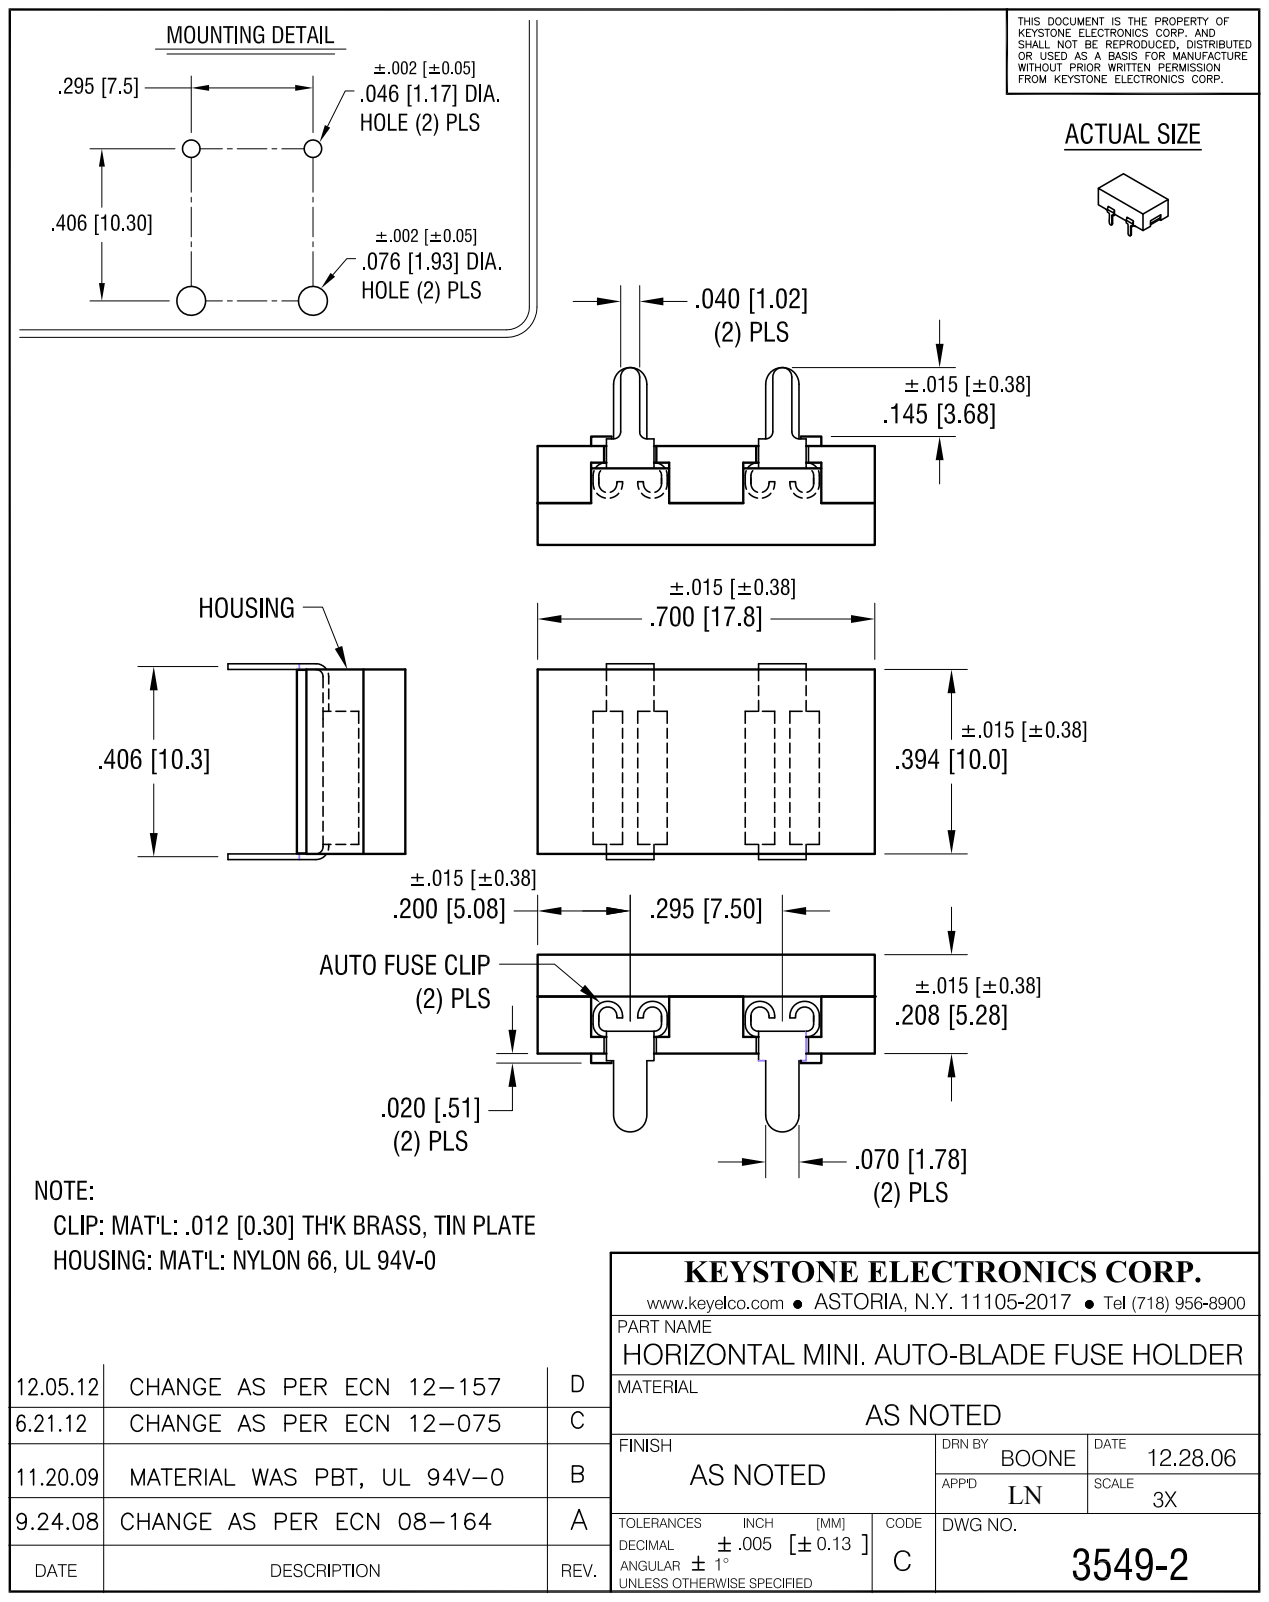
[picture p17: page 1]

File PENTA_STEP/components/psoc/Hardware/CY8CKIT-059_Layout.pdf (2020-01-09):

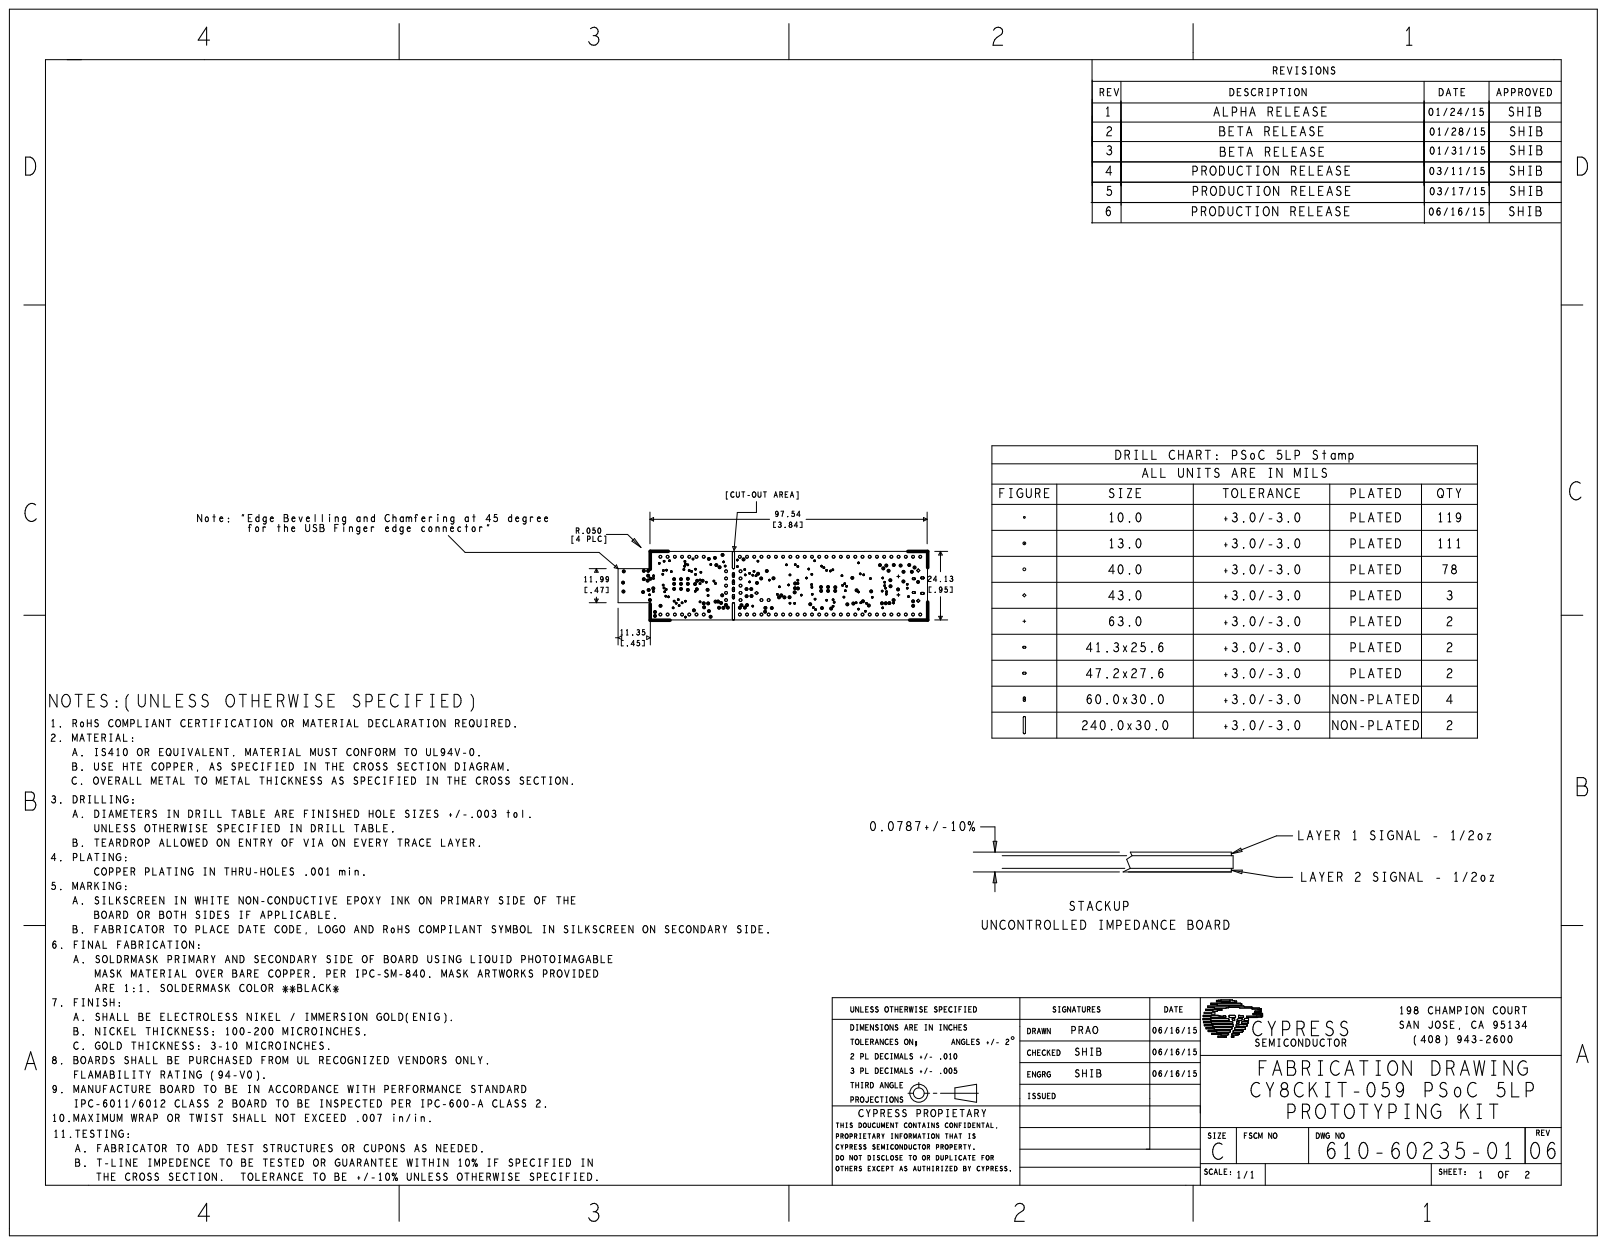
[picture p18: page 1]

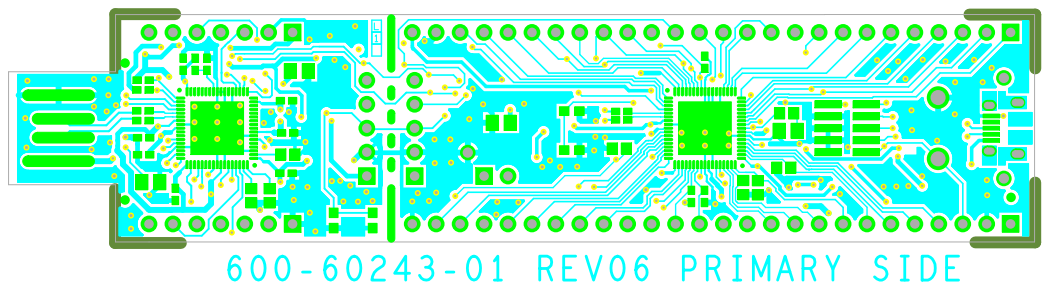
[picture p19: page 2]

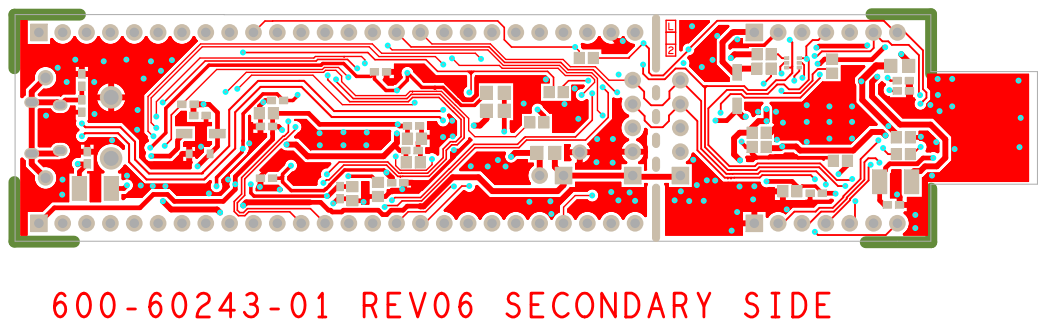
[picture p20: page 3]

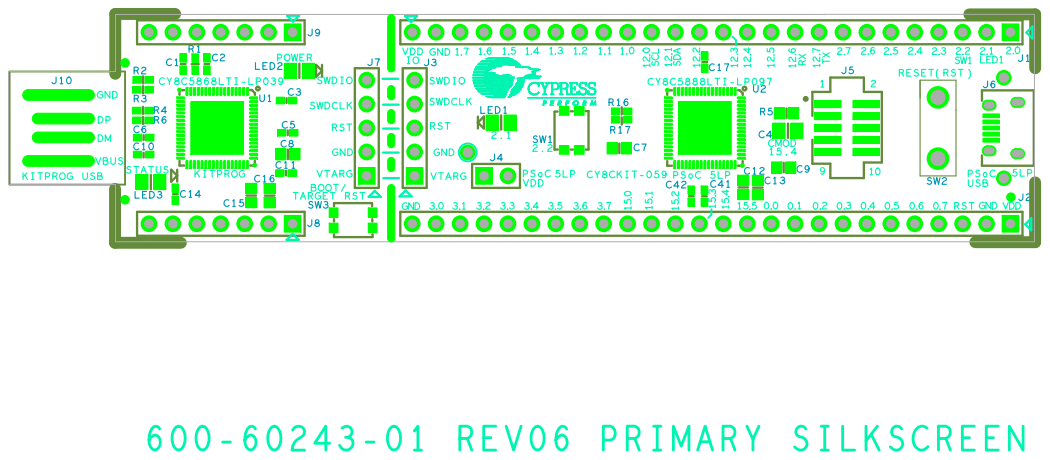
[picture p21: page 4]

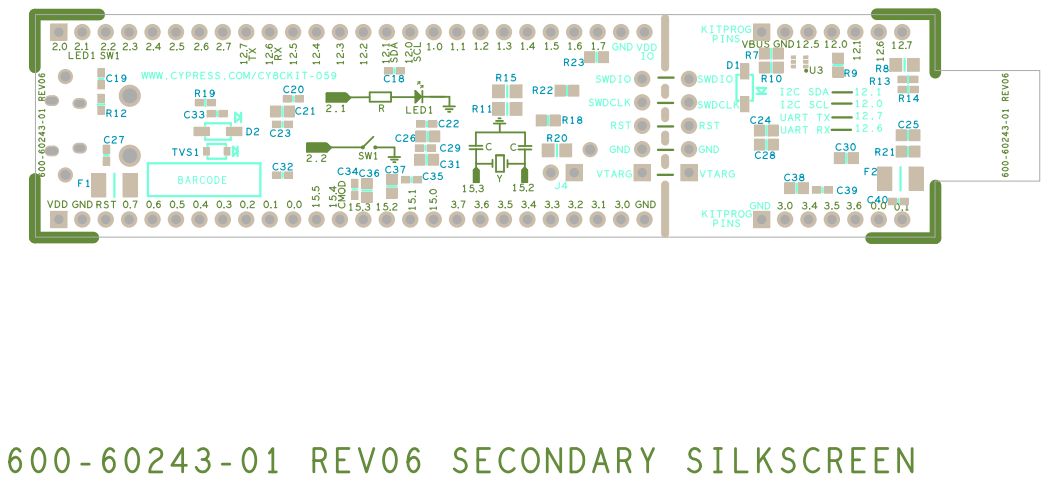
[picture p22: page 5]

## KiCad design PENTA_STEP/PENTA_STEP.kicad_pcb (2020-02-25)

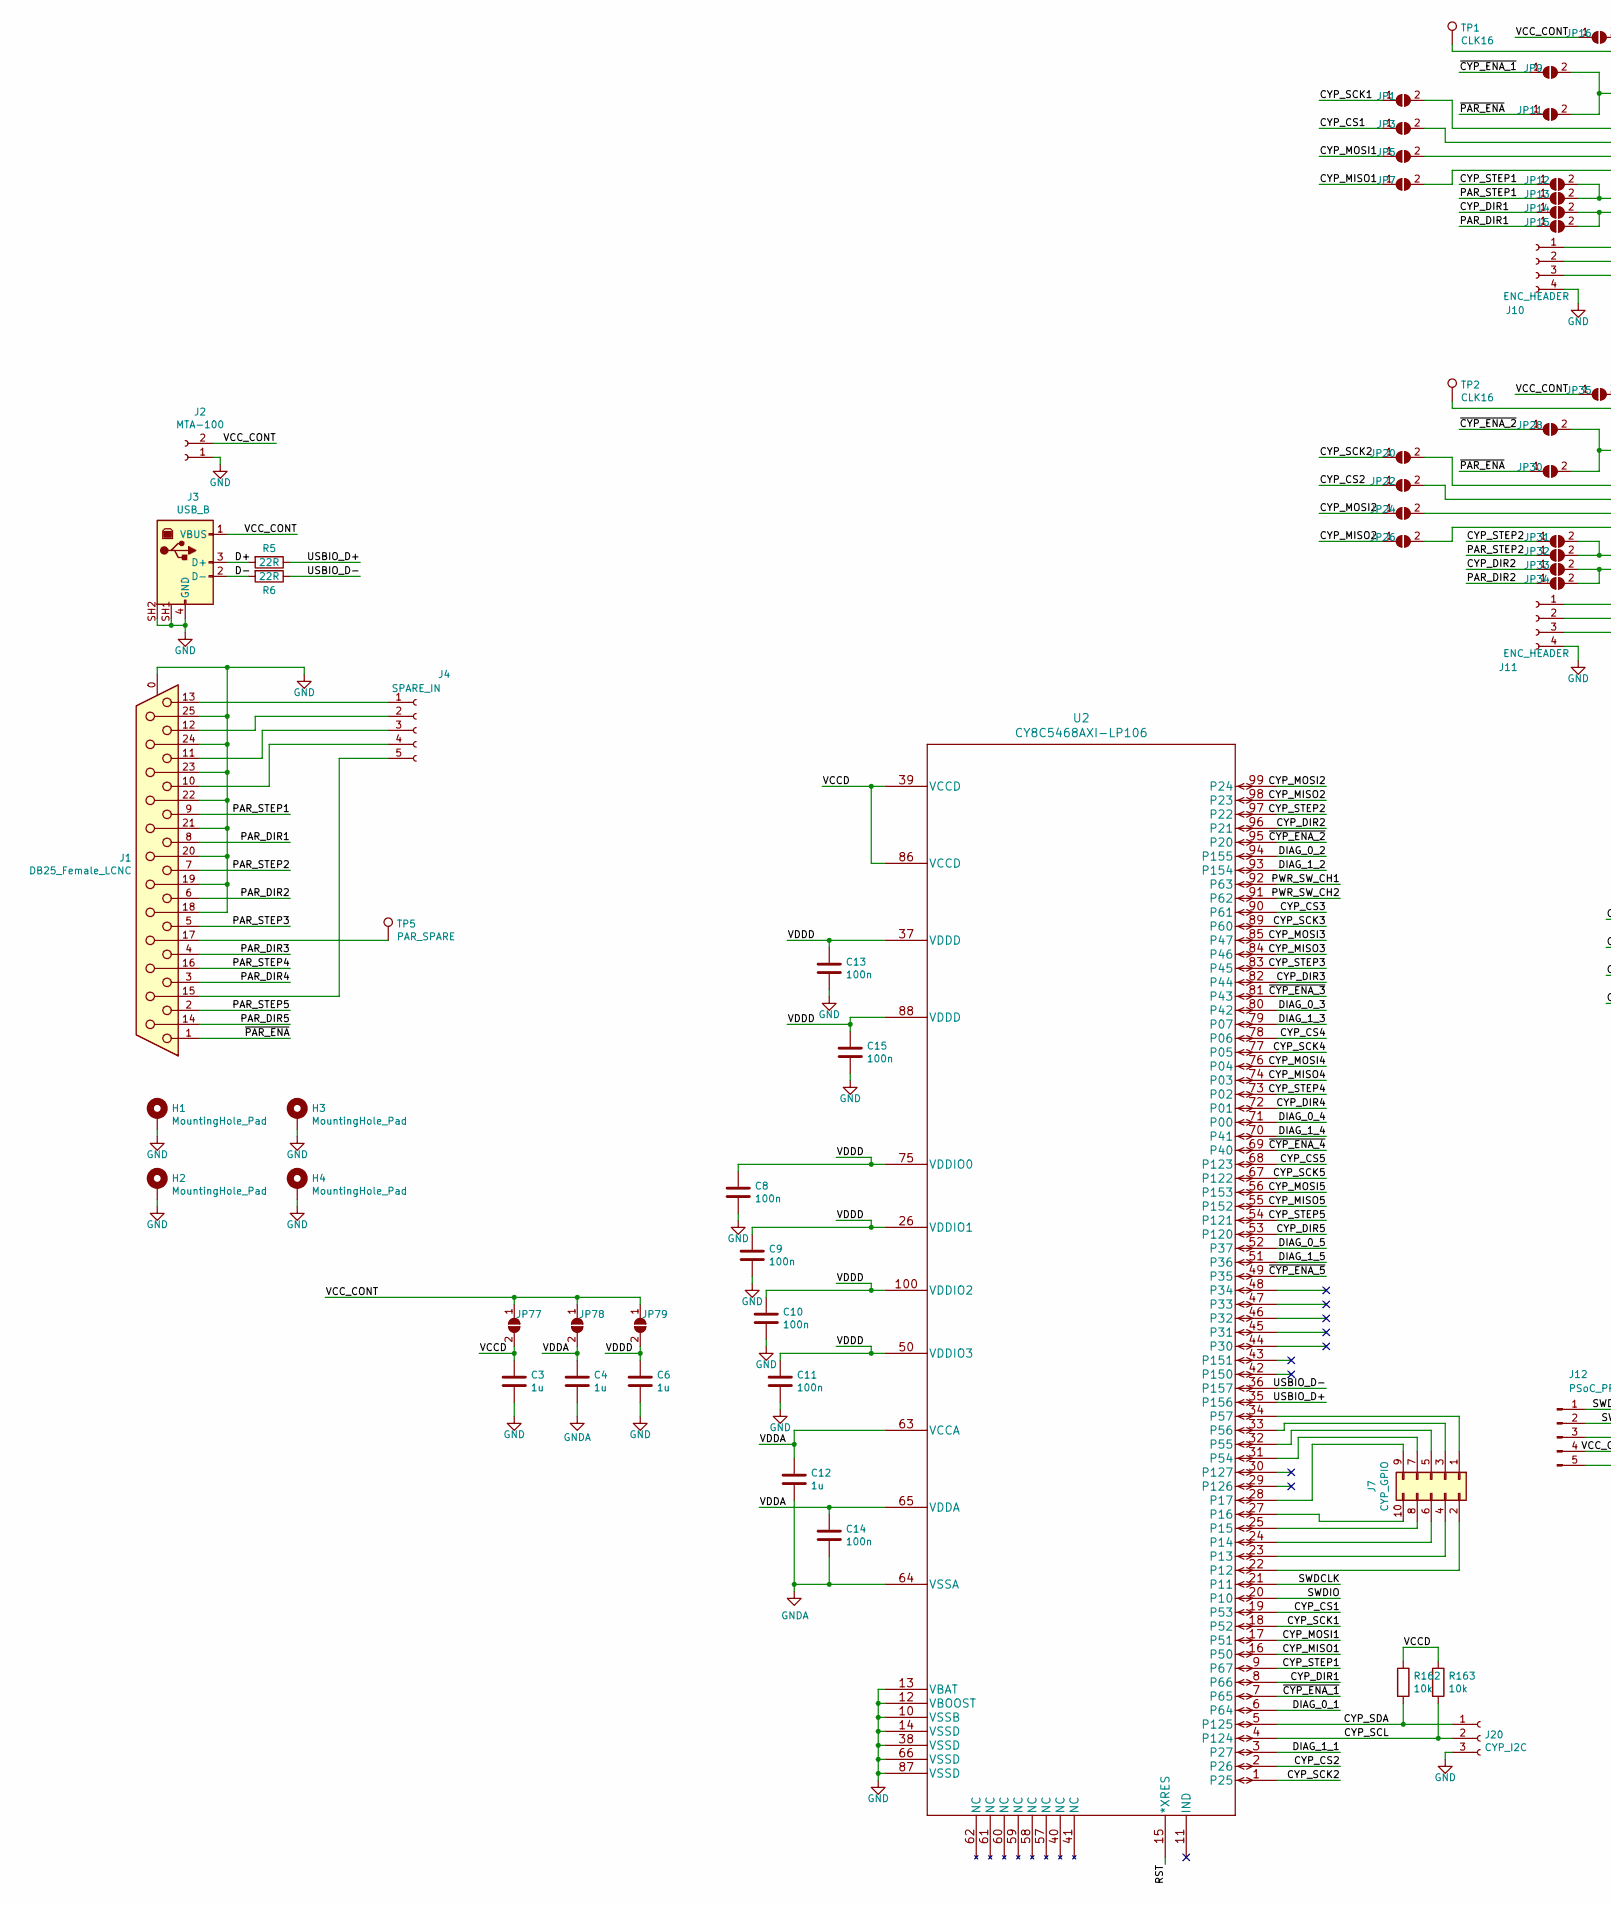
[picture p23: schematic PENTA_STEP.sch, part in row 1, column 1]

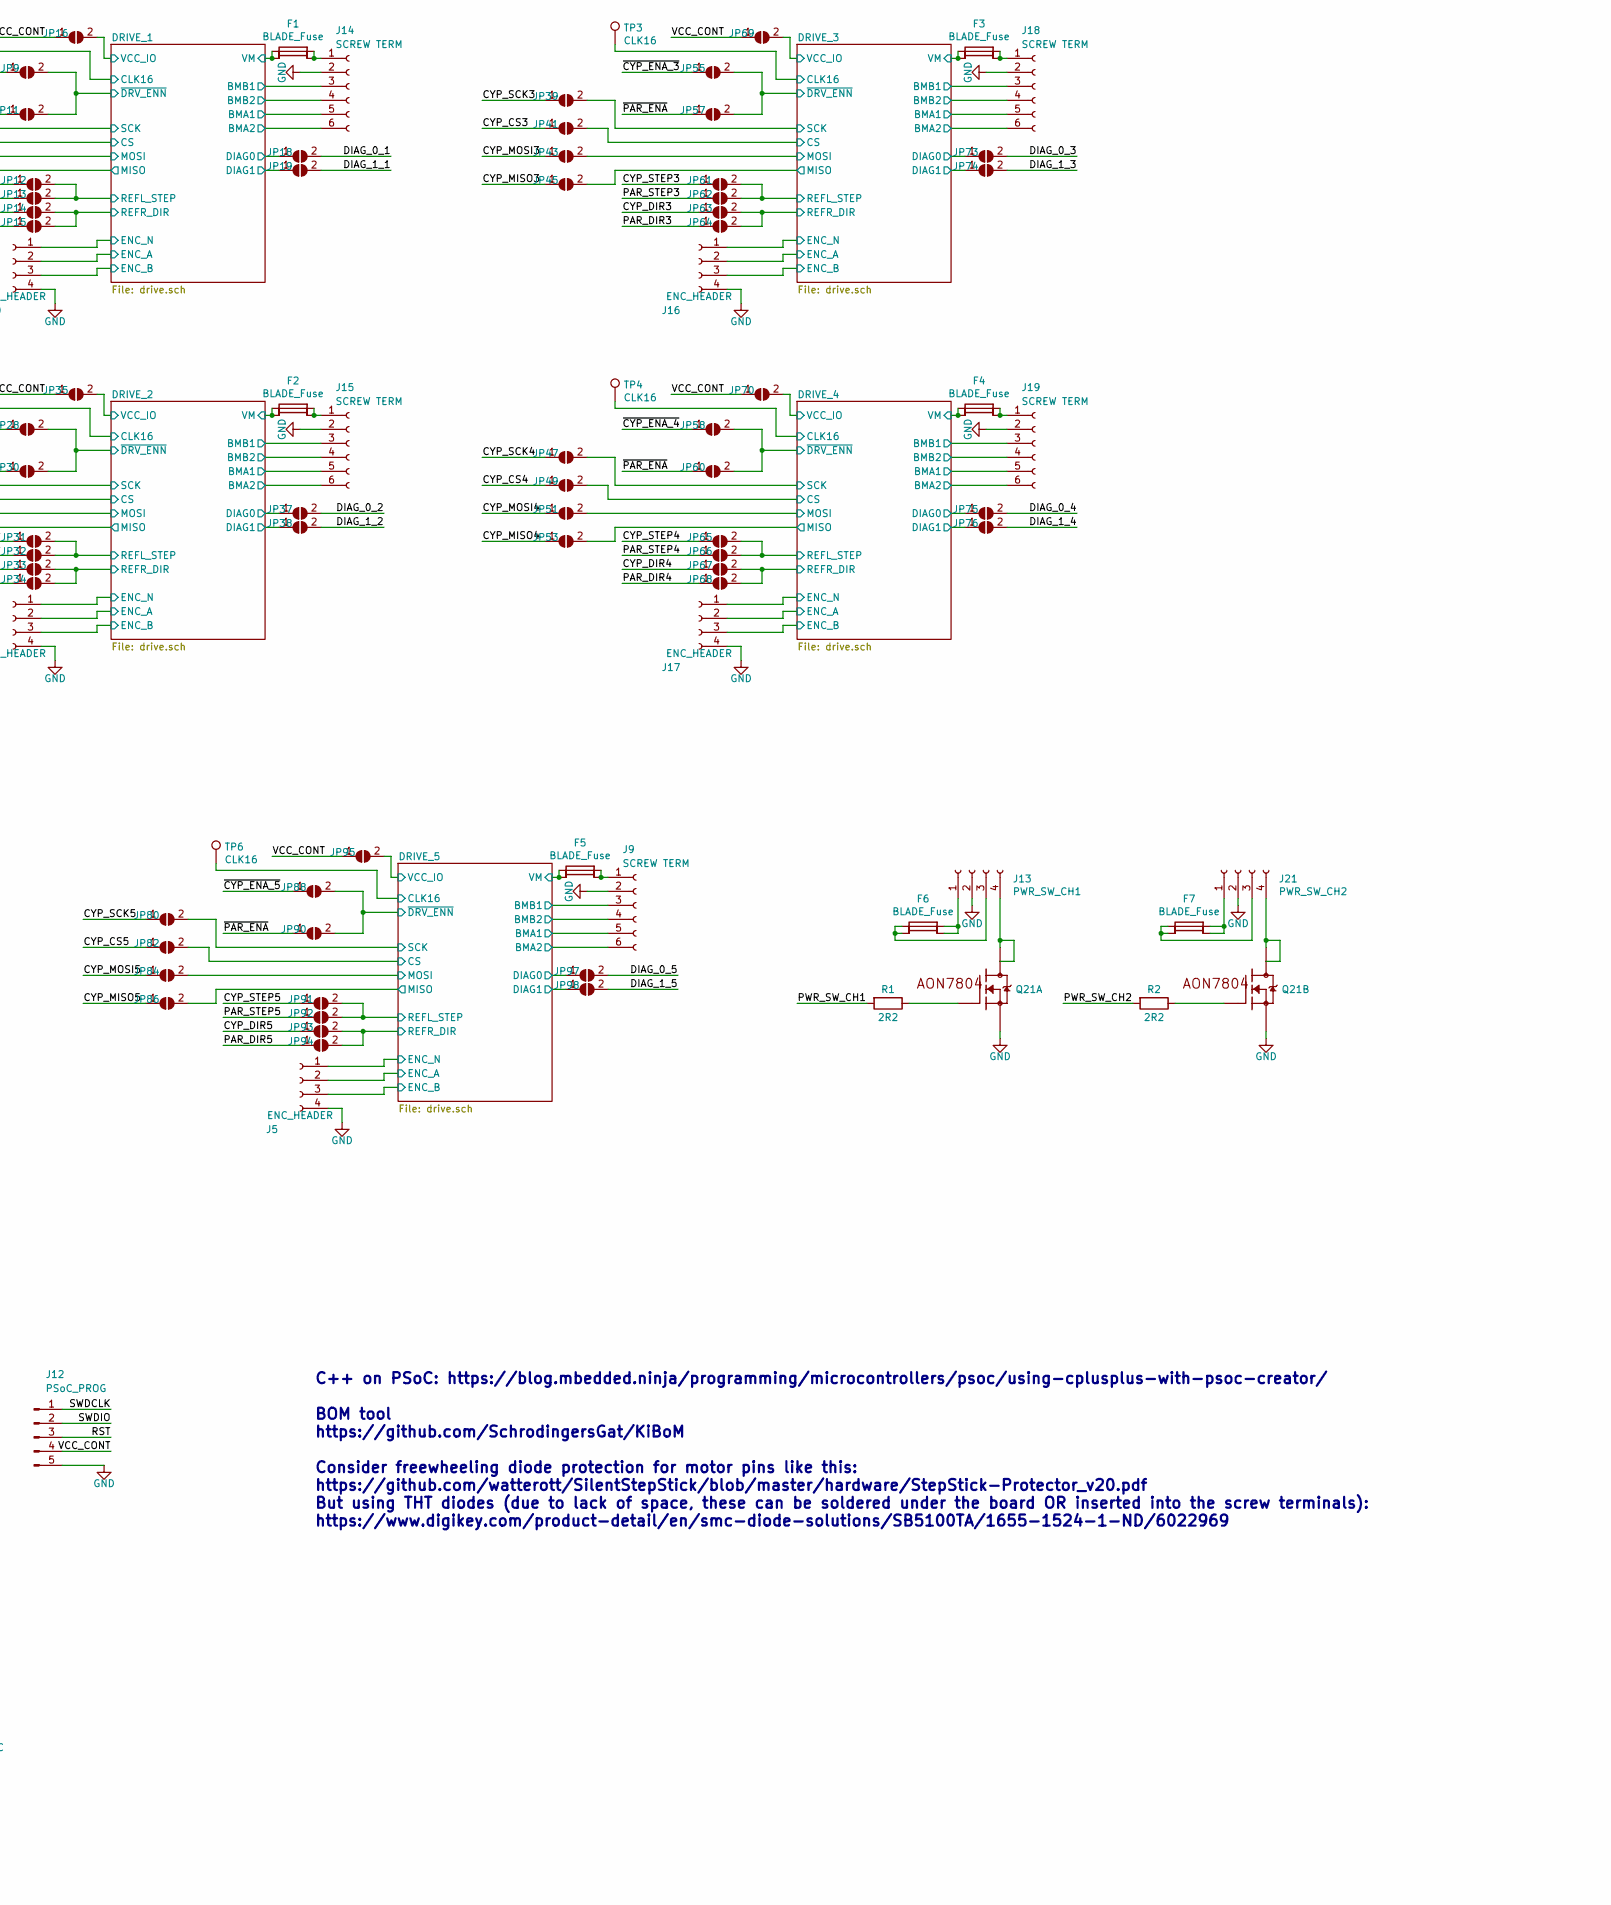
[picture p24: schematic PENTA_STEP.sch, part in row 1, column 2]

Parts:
C3, C4, C6, C12: 1u; C_0603_1608Metric_Pad1.05x0.95mm_HandSolder; MPN CL10B105MO8NNWC
C8, C9, C10, C11, C13, C14, C15: 100n; C_0603_1608Metric_Pad1.05x0.95mm_HandSolder; MPN 06031C104KAT2A
F1, F2, F3, F4, F5: BLADE_Fuse; keystone_3549_2_fuseholder_THT; MPN 3549-2
F6, F7: BLADE_Fuse; keystone_3568_10_fuseholder_THT; MPN 3568-10
H1, H2, H3, H4: MountingHole_Pad; MountingHole_4.5mm_Pad_Via
J1: DB25_Female_LCNC; DSUB-25_Female_Horizontal_P2.77x2.84mm_EdgePinOffset7.70mm_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; MPN DB25-SL-25
J2: MTA-100; 640456-2; MPN 640456-2
J3: USB_B; CUI_UJ2-BH-W1-TH; MPN UJ2-BH-W1-TH
J4: SPARE_IN; PinHeader_1x05_P2.54mm_Vertical
J5, J10, J11, J16, J17: ENC_HEADER; PinHeader_1x04_P1.00mm_Vertical; MPN HDR100MET40M-G-RA-TH
J7: CYP_GPIO; PinHeader_2x05_P2.54mm_Vertical
J9, J14, J15, J18, J19: SCREW TERM; CUI_TB002-500-06BE; MPN TB002-500-06BE
J12: PSoC_PROG; PinHeader_1x05_P2.54mm_Vertical
J13: PWR_SW_CH1; 1776275-4; MPN 1988972
J20: CYP_I2C; PinHeader_1x03_P2.54mm_Vertical
J21: PWR_SW_CH2; 1776275-4; MPN 1988972
JP1, JP3, JP5, JP7, JP9, JP11, JP12, JP13, JP14, JP15, JP16, JP18, JP19, JP20, JP22, JP24, JP26, JP28, JP30, JP31, JP32, JP33, JP34, JP35, JP37, JP38, JP39, JP41, JP43, JP45, JP47, JP49, JP51, JP53, JP55, JP57, JP58, JP60, JP61, JP62, JP63, JP64, JP65, JP66, JP67, JP68, JP69, JP70, JP73, JP74, JP75, JP76, JP77, JP78, JP79, JP80, JP82, JP84, JP86, JP88, JP90, JP91, JP92, JP93, JP94, JP95, JP97, JP98: SolderJumper_2_Open; small_triangle_jumper
Q21: AON7804; DFN3X3_AON7804; MPN AON7804
R1, R2: 2R2; R_0603_1608Metric_Pad1.05x0.95mm_HandSolder; MPN RC0603FR-072R2L
R5, R6: 22R; R_0603_1608Metric_Pad1.05x0.95mm_HandSolder; MPN ERJ-3EKF22R0V
R162, R163: 10k; R_0603_1608Metric_Pad1.05x0.95mm_HandSolder; MPN RC0603JR-0710KL
TP1, TP2, TP3, TP4, TP6: CLK16; TestPoint_Pad_D1.0mm
TP5: PAR_SPARE; TestPoint_Pad_D1.0mm
U2: CY8C5468AXI-LP106; MPN CY8C5468AXI-LP106

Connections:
/CYP_CS1: JP3.1 (A), U2.19 (P53)
/CYP_CS2: JP22.1 (A), U2.2 (P26)
/CYP_CS3: JP41.1 (A), U2.90 (P61)
/CYP_CS4: JP49.1 (A), U2.78 (P06)
/CYP_CS5: JP82.1 (A), U2.68 (P123)
/CYP_DIR1: JP14.1 (A), U2.8 (P66)
/CYP_DIR2: JP33.1 (A), U2.96 (P21)
/CYP_DIR3: JP63.1 (A), U2.82 (P44)
/CYP_DIR4: JP67.1 (A), U2.72 (P01)
/CYP_DIR5: JP93.1 (A), U2.53 (P120)
/CYP_MISO1: JP7.1 (A), U2.16 (P50)
/CYP_MISO2: JP26.1 (A), U2.98 (P23)
/CYP_MISO3: JP45.1 (A), U2.84 (P46)
/CYP_MISO4: JP53.1 (A), U2.74 (P03)
/CYP_MISO5: JP86.1 (A), U2.55 (P152)
/CYP_MOSI1: JP5.1 (A), U2.17 (P51)
/CYP_MOSI2: JP24.1 (A), U2.99 (P24)
/CYP_MOSI3: JP43.1 (A), U2.85 (P47)
/CYP_MOSI4: JP51.1 (A), U2.76 (P04)
/CYP_MOSI5: JP84.1 (A), U2.56 (P153)
/CYP_SCK1: JP1.1 (A), U2.18 (P52)
/CYP_SCK2: JP20.1 (A), U2.1 (P25)
/CYP_SCK3: JP39.1 (A), U2.89 (P60)
/CYP_SCK4: JP47.1 (A), U2.77 (P05)
/CYP_SCK5: JP80.1 (A), U2.67 (P122)
/CYP_SCL: J20.2, R163.2, U2.4 (P124)
/CYP_SDA: J20.1, R162.2, U2.5 (P125)
/CYP_STEP1: JP12.1 (A), U2.9 (P67)
/CYP_STEP2: JP31.1 (A), U2.97 (P22)
/CYP_STEP3: JP61.1 (A), U2.83 (P45)
/CYP_STEP4: JP65.1 (A), U2.73 (P02)
/CYP_STEP5: JP91.1 (A), U2.54 (P121)
/D+: J3.3 (D+), R5.2
/D-: J3.2 (D-), R6.2
/DIAG_0_1: JP18.2 (B), U2.6 (P64)
/DIAG_0_2: JP37.2 (B), U2.94 (P155)
/DIAG_0_3: JP73.2 (B), U2.80 (P42)
/DIAG_0_4: JP75.2 (B), U2.71 (P00)
/DIAG_0_5: JP97.2 (B), U2.52 (P37)
/DIAG_1_1: JP19.2 (B), U2.3 (P27)
/DIAG_1_2: JP38.2 (B), U2.93 (P154)
/DIAG_1_3: JP74.2 (B), U2.79 (P07)
/DIAG_1_4: JP76.2 (B), U2.70 (P41)
/DIAG_1_5: JP98.2 (B), U2.51 (P36)
/DRIVE_1/BMA1: J14.5; also elsewhere on the board
/DRIVE_1/BMA2: J14.6; also elsewhere on the board
/DRIVE_1/BMB1: J14.3; also elsewhere on the board
/DRIVE_1/BMB2: J14.4; also elsewhere on the board
/DRIVE_1/CLK16: TP1.1; also elsewhere on the board
/DRIVE_1/CS: JP3.2 (B); also elsewhere on the board
/DRIVE_1/DIAG0: JP18.1 (A); also elsewhere on the board
/DRIVE_1/DIAG1: JP19.1 (A); also elsewhere on the board
/DRIVE_1/ENC_A: J10.2; also elsewhere on the board
/DRIVE_1/ENC_B: J10.3; also elsewhere on the board
/DRIVE_1/ENC_N: J10.1; also elsewhere on the board
/DRIVE_1/MISO: JP7.2 (B); also elsewhere on the board
/DRIVE_1/MOSI: JP5.2 (B); also elsewhere on the board
/DRIVE_1/REFL_STEP: JP12.2 (B), JP13.2 (B); also elsewhere on the board
/DRIVE_1/REFR_DIR: JP14.2 (B), JP15.2 (B); also elsewhere on the board
/DRIVE_1/SCK: JP1.2 (B); also elsewhere on the board
/DRIVE_1/VCC_IO: JP16.2 (B); also elsewhere on the board
/DRIVE_1/VM: F1.1, F1.2; also elsewhere on the board
/DRIVE_1/~DRV_ENN: JP9.2 (B), JP11.2 (B); also elsewhere on the board
/DRIVE_2/BMA1: J15.5; also elsewhere on the board
/DRIVE_2/BMA2: J15.6; also elsewhere on the board
/DRIVE_2/BMB1: J15.3; also elsewhere on the board
/DRIVE_2/BMB2: J15.4; also elsewhere on the board
/DRIVE_2/CLK16: TP2.1; also elsewhere on the board
/DRIVE_2/CS: JP22.2 (B); also elsewhere on the board
/DRIVE_2/DIAG0: JP37.1 (A); also elsewhere on the board
/DRIVE_2/DIAG1: JP38.1 (A); also elsewhere on the board
/DRIVE_2/ENC_A: J11.2; also elsewhere on the board
/DRIVE_2/ENC_B: J11.3; also elsewhere on the board
/DRIVE_2/ENC_N: J11.1; also elsewhere on the board
/DRIVE_2/MISO: JP26.2 (B); also elsewhere on the board
/DRIVE_2/MOSI: JP24.2 (B); also elsewhere on the board
/DRIVE_2/REFL_STEP: JP31.2 (B), JP32.2 (B); also elsewhere on the board
/DRIVE_2/REFR_DIR: JP33.2 (B), JP34.2 (B); also elsewhere on the board
/DRIVE_2/SCK: JP20.2 (B); also elsewhere on the board
/DRIVE_2/VCC_IO: JP35.2 (B); also elsewhere on the board
/DRIVE_2/VM: F2.1, F2.2; also elsewhere on the board
/DRIVE_2/~DRV_ENN: JP28.2 (B), JP30.2 (B); also elsewhere on the board
/DRIVE_3/BMA1: J18.5; also elsewhere on the board
/DRIVE_3/BMA2: J18.6; also elsewhere on the board
/DRIVE_3/BMB1: J18.3; also elsewhere on the board
/DRIVE_3/BMB2: J18.4; also elsewhere on the board
/DRIVE_3/CLK16: TP3.1; also elsewhere on the board
/DRIVE_3/CS: JP41.2 (B); also elsewhere on the board
/DRIVE_3/DIAG0: JP73.1 (A); also elsewhere on the board
/DRIVE_3/DIAG1: JP74.1 (A); also elsewhere on the board
/DRIVE_3/ENC_A: J16.2; also elsewhere on the board
/DRIVE_3/ENC_B: J16.3; also elsewhere on the board
/DRIVE_3/ENC_N: J16.1; also elsewhere on the board
/DRIVE_3/MISO: JP45.2 (B); also elsewhere on the board
/DRIVE_3/MOSI: JP43.2 (B); also elsewhere on the board
/DRIVE_3/REFL_STEP: JP61.2 (B), JP62.2 (B); also elsewhere on the board
/DRIVE_3/REFR_DIR: JP63.2 (B), JP64.2 (B); also elsewhere on the board
/DRIVE_3/SCK: JP39.2 (B); also elsewhere on the board
/DRIVE_3/VCC_IO: JP69.2 (B); also elsewhere on the board
/DRIVE_3/VM: F3.1, F3.2; also elsewhere on the board
/DRIVE_3/~DRV_ENN: JP55.2 (B), JP57.2 (B); also elsewhere on the board
/DRIVE_4/BMA1: J19.5; also elsewhere on the board
/DRIVE_4/BMA2: J19.6; also elsewhere on the board
/DRIVE_4/BMB1: J19.3; also elsewhere on the board
/DRIVE_4/BMB2: J19.4; also elsewhere on the board
/DRIVE_4/CLK16: TP4.1; also elsewhere on the board
/DRIVE_4/CS: JP49.2 (B); also elsewhere on the board
/DRIVE_4/DIAG0: JP75.1 (A); also elsewhere on the board
/DRIVE_4/DIAG1: JP76.1 (A); also elsewhere on the board
/DRIVE_4/ENC_A: J17.2; also elsewhere on the board
/DRIVE_4/ENC_B: J17.3; also elsewhere on the board
/DRIVE_4/ENC_N: J17.1; also elsewhere on the board
/DRIVE_4/MISO: JP53.2 (B); also elsewhere on the board
/DRIVE_4/MOSI: JP51.2 (B); also elsewhere on the board
/DRIVE_4/REFL_STEP: JP65.2 (B), JP66.2 (B); also elsewhere on the board
/DRIVE_4/REFR_DIR: JP67.2 (B), JP68.2 (B); also elsewhere on the board
/DRIVE_4/SCK: JP47.2 (B); also elsewhere on the board
/DRIVE_4/VCC_IO: JP70.2 (B); also elsewhere on the board
/DRIVE_4/VM: F4.1, F4.2; also elsewhere on the board
/DRIVE_4/~DRV_ENN: JP58.2 (B), JP60.2 (B); also elsewhere on the board
/DRIVE_5/BMA1: J9.5; also elsewhere on the board
/DRIVE_5/BMA2: J9.6; also elsewhere on the board
/DRIVE_5/BMB1: J9.3; also elsewhere on the board
/DRIVE_5/BMB2: J9.4; also elsewhere on the board
/DRIVE_5/CLK16: TP6.1; also elsewhere on the board
/DRIVE_5/CS: JP82.2 (B); also elsewhere on the board
/DRIVE_5/DIAG0: JP97.1 (A); also elsewhere on the board
/DRIVE_5/DIAG1: JP98.1 (A); also elsewhere on the board
/DRIVE_5/ENC_A: J5.2; also elsewhere on the board
/DRIVE_5/ENC_B: J5.3; also elsewhere on the board
/DRIVE_5/ENC_N: J5.1; also elsewhere on the board
/DRIVE_5/MISO: JP86.2 (B); also elsewhere on the board
/DRIVE_5/MOSI: JP84.2 (B); also elsewhere on the board
/DRIVE_5/REFL_STEP: JP91.2 (B), JP92.2 (B); also elsewhere on the board
/DRIVE_5/REFR_DIR: JP93.2 (B), JP94.2 (B); also elsewhere on the board
/DRIVE_5/SCK: JP80.2 (B); also elsewhere on the board
/DRIVE_5/VCC_IO: JP95.2 (B); also elsewhere on the board
/DRIVE_5/VM: F5.1, F5.2; also elsewhere on the board
/DRIVE_5/~DRV_ENN: JP88.2 (B), JP90.2 (B); also elsewhere on the board
/PAR_DIR1: J1.8, JP15.1 (A)
/PAR_DIR2: J1.6, JP34.1 (A)
/PAR_DIR3: J1.4, JP64.1 (A)
/PAR_DIR4: J1.3, JP68.1 (A)
/PAR_DIR5: J1.14, JP94.1 (A)
/PAR_STEP1: J1.9, JP13.1 (A)
/PAR_STEP2: J1.7, JP32.1 (A)
/PAR_STEP3: J1.5, JP62.1 (A)
/PAR_STEP4: J1.16, JP66.1 (A)
/PAR_STEP5: J1.2, JP92.1 (A)
/PWR_SW_CH1: R1.2, U2.92 (P63)
/PWR_SW_CH2: R2.2, U2.91 (P62)
/RST: J12.3, U2.15 (*XRES)
/SWDCLK: J12.1, U2.21 (P11)
/SWDIO: J12.2, U2.20 (P10)
/USBIO_D+: R5.1, U2.35 (P156)
/USBIO_D-: R6.1, U2.36 (P157)
/VCCD: C3.1, JP77.2 (B), R162.1, R163.1, U2.39 (VCCD), U2.86 (VCCD)
/VCC_CONT: J2.2, J3.1 (VBUS), J12.4, JP16.1 (A), JP35.1 (A), JP69.1 (A), JP70.1 (A), JP77.1 (A), JP78.1 (A), JP79.1 (A), JP95.1 (A)
/VDDA: C4.1, C12.1, C14.1, JP78.2 (B), U2.63 (VCCA), U2.65 (VDDA)
/VDDD: C6.1, C8.1, C9.1, C10.1, C11.1, C13.1, C15.1, JP79.2 (B), U2.26 (VDDIO1), U2.37 (VDDD), U2.50 (VDDIO3), U2.75 (VDDIO0), U2.88 (VDDD), U2.100 (VDDIO2)
/~CYP_ENA_1: JP9.1 (A), U2.7 (P65)
/~CYP_ENA_2: JP28.1 (A), U2.95 (P20)
/~CYP_ENA_3: JP55.1 (A), U2.81 (P43)
/~CYP_ENA_4: JP58.1 (A), U2.69 (P40)
/~CYP_ENA_5: JP88.1 (A), U2.49 (P35)
/~PAR_ENA: J1.1, JP11.1 (A), JP30.1 (A), JP57.1 (A), JP60.1 (A), JP90.1 (A)
GND: C3.2, C6.2, C8.2, C9.2, C10.2, C11.2, C13.2, C15.2, H1.1, H2.1, H3.1, H4.1, J1.0 (PAD), J1.18, J1.19, J1.20, J1.21, J1.22, J1.23, J1.24, J1.25, J2.1, J3.4 (GND), J3.SH1, J3.SH2, J5.4, J9.2, J10.4, J11.4, J12.5, J13.2, J14.2, J15.2, J16.4, J17.4, J18.2, J19.2, J20.3, J21.2, Q21.S1 (S), Q21.S2 (S), U2.10 (VSSB), U2.12 (VBOOST), U2.13 (VBAT), U2.14 (VSSD), U2.38 (VSSD), U2.66 (VSSD), U2.87 (VSSD); also elsewhere on the board
GNDA: C4.2, C12.2, C14.2, U2.64 (VSSA)
unnamed: F1.3, F1.4, J14.1
unnamed: F2.3, F2.4, J15.1
unnamed: F3.3, F3.4, J18.1
unnamed: F4.3, F4.4, J19.1
unnamed: F5.3, F5.4, J9.1
unnamed: F6.1, F6.2, J13.3
unnamed: F6.3, F6.4, J13.1
unnamed: F7.1, F7.2, J21.3
unnamed: F7.3, F7.4, J21.1
unnamed: J1.10, J4.4
unnamed: J1.11, J4.3
unnamed: J1.12, J4.2
unnamed: J1.13, J4.1
unnamed: J1.15, J4.5
unnamed: J1.17, TP5.1
unnamed: J7.1, U2.34 (P57)
unnamed: J7.2, U2.22 (P12)
unnamed: J7.3, U2.33 (P56)
unnamed: J7.4, U2.23 (P13)
unnamed: J7.5, U2.32 (P55)
unnamed: J7.6, U2.24 (P14)
unnamed: J7.7, U2.31 (P54)
unnamed: J7.8, U2.25 (P15)
unnamed: J7.9, U2.28 (P17)
unnamed: J7.10, U2.27 (P16)
unnamed: J13.4, Q21.D1 (D), Q21.D1A (D1)
unnamed: J21.4, Q21.D2 (D), Q21.D2A (D1)
unnamed: Q21.G1 (G), R1.1
unnamed: Q21.G2 (G), R2.1

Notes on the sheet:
C++ on PSoC: https://blog.mbedded.ninja/programming/microcontrollers/psoc/using-cplusplus-with-psoc-creator/ BOM tool https://github.com/SchrodingersGat/KiBoM Consider freewheeling diode protection for motor pins like this: https://github.com/watterott/SilentStepStick/blob/master/hardware/StepStick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

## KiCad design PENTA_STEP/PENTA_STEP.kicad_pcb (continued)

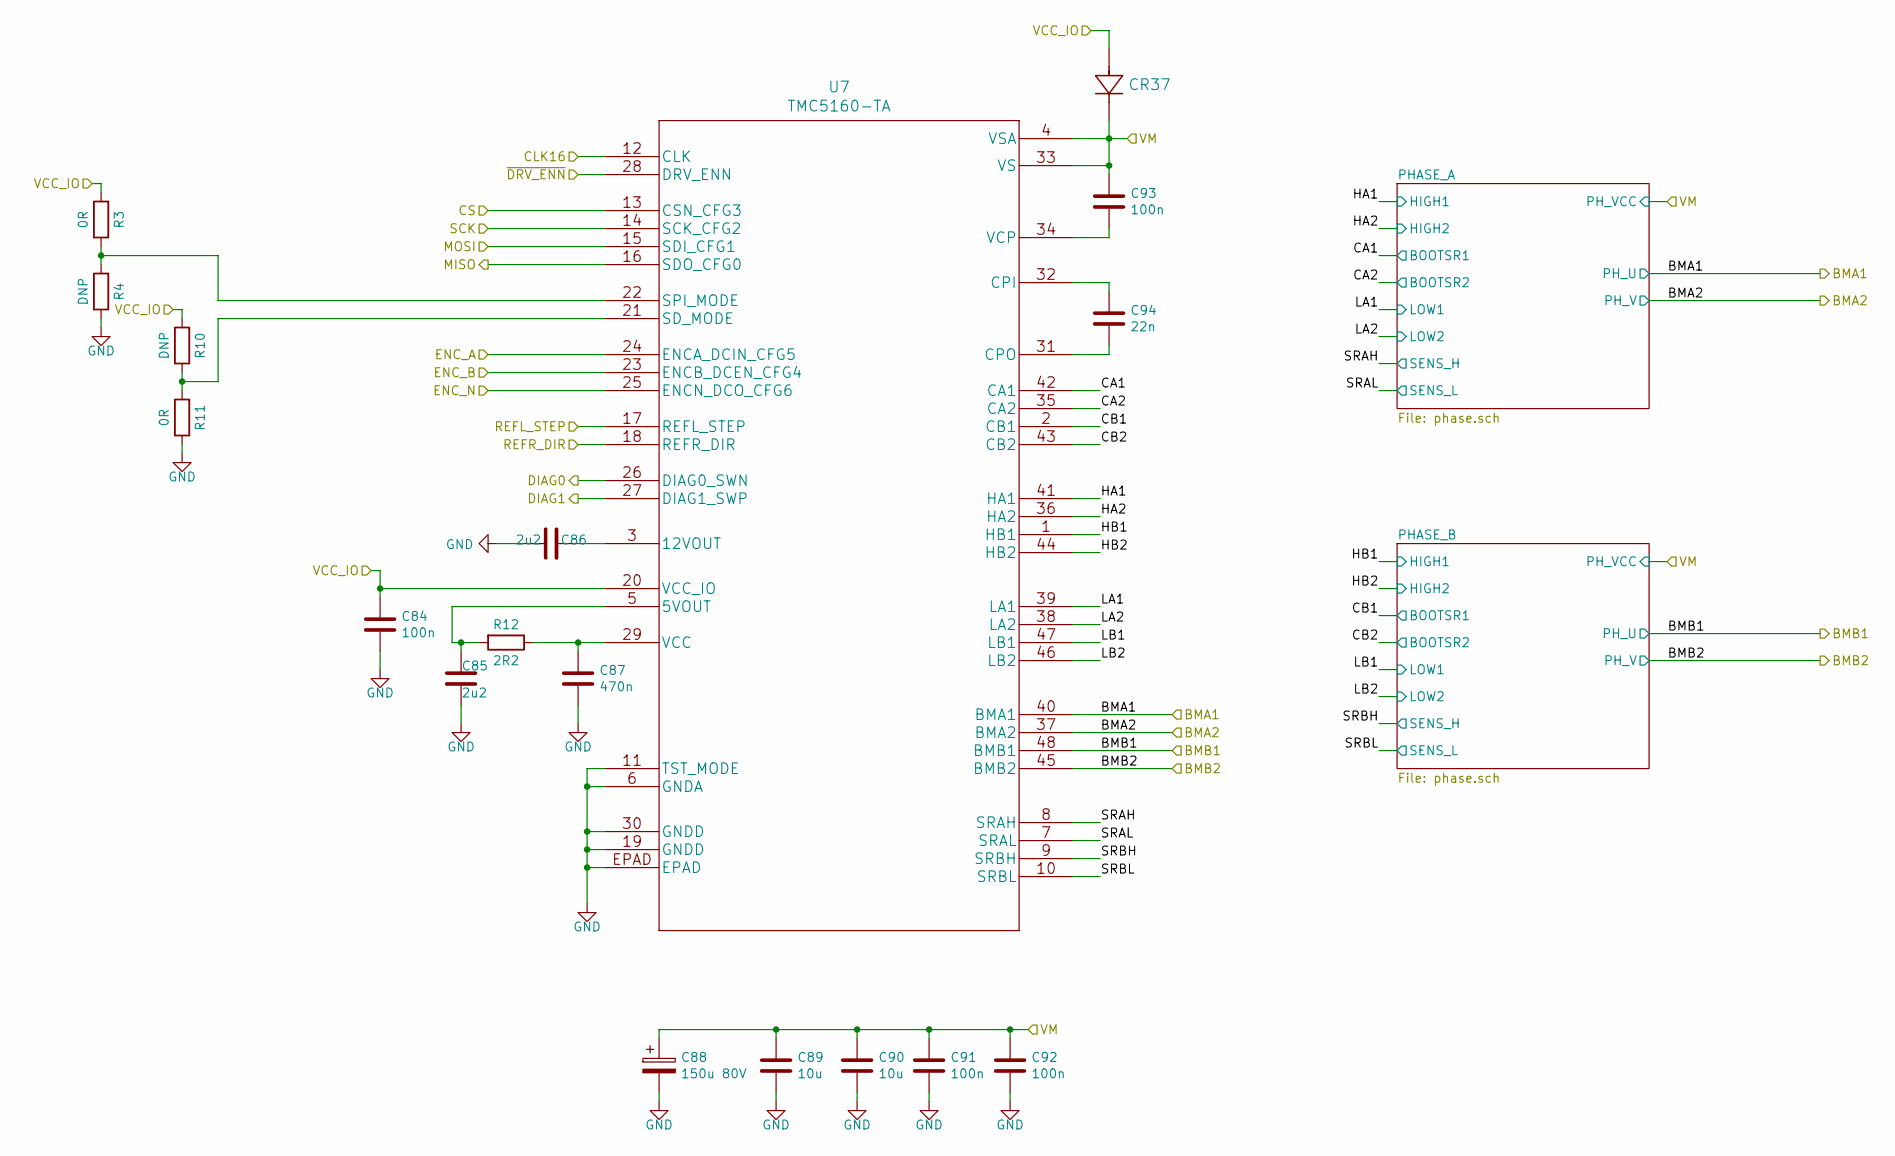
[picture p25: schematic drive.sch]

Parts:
C16, C23, C24, C25: 100n; C_0603_1608Metric_Pad1.05x0.95mm_HandSolder; MPN 06031C104KAT2A
C17, C18: 2u2; C_0603_1608Metric_Pad1.05x0.95mm_HandSolder; MPN CL10A225KO8NNNC
C19: 470n; C_0603_1608Metric_Pad1.05x0.95mm_HandSolder; MPN 885012106008
C20: 150u 80V; CAPAE1350X1400N_EEVFK1J151Q; MPN EEV-FK1K151Q
C21, C22: 10u; C_1210_3225Metric_Pad1.42x2.65mm_HandSolder; MPN C3225X7R1N106M250AC
C26: 22n; C_0603_1608Metric_Pad1.05x0.95mm_HandSolder; MPN CL10B223KB8NNNC
CR1: PMEG6010CEGWX; MPN S310FA
R86, R89: 0R; R_0603_1608Metric_Pad1.05x0.95mm_HandSolder; MPN RC0603JR-070RL
R87, R88: DNP; R_0603_1608Metric_Pad1.05x0.95mm_HandSolder; MPN RC0603JR-070RL
R90: 2R2; R_0603_1608Metric_Pad1.05x0.95mm_HandSolder; MPN RC0603FR-072R2L
U3: TMC5160-TA; MPN TMC5160-TA

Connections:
/DRIVE_1/BMA1: U3.40 (BMA1); also elsewhere on the board
/DRIVE_1/BMA2: U3.37 (BMA2); also elsewhere on the board
/DRIVE_1/BMB1: U3.48 (BMB1); also elsewhere on the board
/DRIVE_1/BMB2: U3.45 (BMB2); also elsewhere on the board
/DRIVE_1/CA1: U3.42 (CA1); also elsewhere on the board
/DRIVE_1/CA2: U3.35 (CA2); also elsewhere on the board
/DRIVE_1/CB1: U3.2 (CB1); also elsewhere on the board
/DRIVE_1/CB2: U3.43 (CB2); also elsewhere on the board
/DRIVE_1/CLK16: U3.12 (CLK); also elsewhere on the board
/DRIVE_1/CS: U3.13 (CSN_CFG3); also elsewhere on the board
/DRIVE_1/DIAG0: U3.26 (DIAG0_SWN); also elsewhere on the board
/DRIVE_1/DIAG1: U3.27 (DIAG1_SWP); also elsewhere on the board
/DRIVE_1/ENC_A: U3.24 (ENCA_DCIN_CFG5); also elsewhere on the board
/DRIVE_1/ENC_B: U3.23 (ENCB_DCEN_CFG4); also elsewhere on the board
/DRIVE_1/ENC_N: U3.25 (ENCN_DCO_CFG6); also elsewhere on the board
/DRIVE_1/HA1: U3.41 (HA1); also elsewhere on the board
/DRIVE_1/HA2: U3.36 (HA2); also elsewhere on the board
/DRIVE_1/HB1: U3.1 (HB1); also elsewhere on the board
/DRIVE_1/HB2: U3.44 (HB2); also elsewhere on the board
/DRIVE_1/LA1: U3.39 (LA1); also elsewhere on the board
/DRIVE_1/LA2: U3.38 (LA2); also elsewhere on the board
/DRIVE_1/LB1: U3.47 (LB1); also elsewhere on the board
/DRIVE_1/LB2: U3.46 (LB2); also elsewhere on the board
/DRIVE_1/MISO: U3.16 (SDO_CFG0); also elsewhere on the board
/DRIVE_1/MOSI: U3.15 (SDI_CFG1); also elsewhere on the board
/DRIVE_1/REFL_STEP: U3.17 (REFL_STEP); also elsewhere on the board
/DRIVE_1/REFR_DIR: U3.18 (REFR_DIR); also elsewhere on the board
/DRIVE_1/SCK: U3.14 (SCK_CFG2); also elsewhere on the board
/DRIVE_1/SRAH: U3.8 (SRAH); also elsewhere on the board
/DRIVE_1/SRAL: U3.7 (SRAL); also elsewhere on the board
/DRIVE_1/SRBH: U3.9 (SRBH); also elsewhere on the board
/DRIVE_1/SRBL: U3.10 (SRBL); also elsewhere on the board
/DRIVE_1/VCC_IO: C16.1, CR1.2, R86.2, R88.2, U3.20 (VCC_IO); also elsewhere on the board
/DRIVE_1/VM: C20.1, C21.1, C22.1, C23.1, C24.1, C25.1, CR1.1, U3.4 (VSA), U3.33 (VS); also elsewhere on the board
/DRIVE_1/~DRV_ENN: U3.28 (DRV_ENN); also elsewhere on the board
GND: C16.2, C17.1, C18.1, C19.2, C20.2, C21.2, C22.2, C23.2, C24.2, R87.1, R89.1, U3.6 (GNDA), U3.11 (TST_MODE), U3.19 (GNDD), U3.30 (GNDD), U3.EPAD; also elsewhere on the board
unnamed: C17.2, R90.2, U3.5 (5VOUT)
unnamed: C18.2, U3.3 (12VOUT)
unnamed: C19.1, R90.1, U3.29 (VCC)
unnamed: C25.2, U3.34 (VCP)
unnamed: C26.1, U3.32 (CPI)
unnamed: C26.2, U3.31 (CPO)
unnamed: R86.1, R87.2, U3.22 (SPI_MODE)
unnamed: R88.1, R89.2, U3.21 (SD_MODE)

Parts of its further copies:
C33, C40, C41, C42, C50, C57, C58, C59, C67, C74, C75, C76, C84, C91, C92, C93: 100n; C_0603_1608Metric_Pad1.05x0.95mm_HandSolder; MPN 06031C104KAT2A
C34, C35, C51, C52, C68, C69, C85, C86: 2u2; C_0603_1608Metric_Pad1.05x0.95mm_HandSolder; MPN CL10A225KO8NNNC
C36, C53, C70, C87: 470n; C_0603_1608Metric_Pad1.05x0.95mm_HandSolder; MPN 885012106008
C37, C54, C71, C88: 150u 80V; CAPAE1350X1400N_EEVFK1J151Q; MPN EEV-FK1K151Q
C38, C39, C55, C56, C72, C73, C89, C90: 10u; C_1210_3225Metric_Pad1.42x2.65mm_HandSolder; MPN C3225X7R1N106M250AC
C43, C60, C77, C94: 22n; C_0603_1608Metric_Pad1.05x0.95mm_HandSolder; MPN CL10B223KB8NNNC
CR10, CR19, CR28, CR37: PMEG6010CEGWX; MPN S310FA
R3, R11, R105, R108, R124, R127, R143, R146: 0R; R_0603_1608Metric_Pad1.05x0.95mm_HandSolder; MPN RC0603JR-070RL
R4, R10, R106, R107, R125, R126, R144, R145: DNP; R_0603_1608Metric_Pad1.05x0.95mm_HandSolder; MPN RC0603JR-070RL
R12, R109, R128, R147: 2R2; R_0603_1608Metric_Pad1.05x0.95mm_HandSolder; MPN RC0603FR-072R2L
U4, U5, U6, U7: TMC5160-TA; MPN TMC5160-TA

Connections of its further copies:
/DRIVE_2/BMA1: U4.40 (BMA1); also elsewhere on the board
/DRIVE_2/BMA2: U4.37 (BMA2); also elsewhere on the board
/DRIVE_2/BMB1: U4.48 (BMB1); also elsewhere on the board
/DRIVE_2/BMB2: U4.45 (BMB2); also elsewhere on the board
/DRIVE_2/CA1: U4.42 (CA1); also elsewhere on the board
/DRIVE_2/CA2: U4.35 (CA2); also elsewhere on the board
/DRIVE_2/CB1: U4.2 (CB1); also elsewhere on the board
/DRIVE_2/CB2: U4.43 (CB2); also elsewhere on the board
/DRIVE_2/CLK16: U4.12 (CLK); also elsewhere on the board
/DRIVE_2/CS: U4.13 (CSN_CFG3); also elsewhere on the board
/DRIVE_2/DIAG0: U4.26 (DIAG0_SWN); also elsewhere on the board
/DRIVE_2/DIAG1: U4.27 (DIAG1_SWP); also elsewhere on the board
/DRIVE_2/ENC_A: U4.24 (ENCA_DCIN_CFG5); also elsewhere on the board
/DRIVE_2/ENC_B: U4.23 (ENCB_DCEN_CFG4); also elsewhere on the board
/DRIVE_2/ENC_N: U4.25 (ENCN_DCO_CFG6); also elsewhere on the board
/DRIVE_2/HA1: U4.41 (HA1); also elsewhere on the board
/DRIVE_2/HA2: U4.36 (HA2); also elsewhere on the board
/DRIVE_2/HB1: U4.1 (HB1); also elsewhere on the board
/DRIVE_2/HB2: U4.44 (HB2); also elsewhere on the board
/DRIVE_2/LA1: U4.39 (LA1); also elsewhere on the board
/DRIVE_2/LA2: U4.38 (LA2); also elsewhere on the board
/DRIVE_2/LB1: U4.47 (LB1); also elsewhere on the board
/DRIVE_2/LB2: U4.46 (LB2); also elsewhere on the board
/DRIVE_2/MISO: U4.16 (SDO_CFG0); also elsewhere on the board
/DRIVE_2/MOSI: U4.15 (SDI_CFG1); also elsewhere on the board
/DRIVE_2/REFL_STEP: U4.17 (REFL_STEP); also elsewhere on the board
/DRIVE_2/REFR_DIR: U4.18 (REFR_DIR); also elsewhere on the board
/DRIVE_2/SCK: U4.14 (SCK_CFG2); also elsewhere on the board
/DRIVE_2/SRAH: U4.8 (SRAH); also elsewhere on the board
/DRIVE_2/SRAL: U4.7 (SRAL); also elsewhere on the board
/DRIVE_2/SRBH: U4.9 (SRBH); also elsewhere on the board
/DRIVE_2/SRBL: U4.10 (SRBL); also elsewhere on the board
/DRIVE_2/VCC_IO: C33.1, CR10.2, R105.2, R107.2, U4.20 (VCC_IO); also elsewhere on the board
/DRIVE_2/VM: C37.1, C38.1, C39.1, C40.1, C41.1, C42.1, CR10.1, U4.4 (VSA), U4.33 (VS); also elsewhere on the board
/DRIVE_2/~DRV_ENN: U4.28 (DRV_ENN); also elsewhere on the board
/DRIVE_3/BMA1: U5.40 (BMA1); also elsewhere on the board
/DRIVE_3/BMA2: U5.37 (BMA2); also elsewhere on the board
/DRIVE_3/BMB1: U5.48 (BMB1); also elsewhere on the board
/DRIVE_3/BMB2: U5.45 (BMB2); also elsewhere on the board
/DRIVE_3/CA1: U5.42 (CA1); also elsewhere on the board
/DRIVE_3/CA2: U5.35 (CA2); also elsewhere on the board
/DRIVE_3/CB1: U5.2 (CB1); also elsewhere on the board
/DRIVE_3/CB2: U5.43 (CB2); also elsewhere on the board
/DRIVE_3/CLK16: U5.12 (CLK); also elsewhere on the board
/DRIVE_3/CS: U5.13 (CSN_CFG3); also elsewhere on the board
/DRIVE_3/DIAG0: U5.26 (DIAG0_SWN); also elsewhere on the board
/DRIVE_3/DIAG1: U5.27 (DIAG1_SWP); also elsewhere on the board
/DRIVE_3/ENC_A: U5.24 (ENCA_DCIN_CFG5); also elsewhere on the board
/DRIVE_3/ENC_B: U5.23 (ENCB_DCEN_CFG4); also elsewhere on the board
/DRIVE_3/ENC_N: U5.25 (ENCN_DCO_CFG6); also elsewhere on the board
/DRIVE_3/HA1: U5.41 (HA1); also elsewhere on the board
/DRIVE_3/HA2: U5.36 (HA2); also elsewhere on the board
/DRIVE_3/HB1: U5.1 (HB1); also elsewhere on the board
/DRIVE_3/HB2: U5.44 (HB2); also elsewhere on the board
/DRIVE_3/LA1: U5.39 (LA1); also elsewhere on the board
/DRIVE_3/LA2: U5.38 (LA2); also elsewhere on the board
/DRIVE_3/LB1: U5.47 (LB1); also elsewhere on the board
/DRIVE_3/LB2: U5.46 (LB2); also elsewhere on the board
/DRIVE_3/MISO: U5.16 (SDO_CFG0); also elsewhere on the board
/DRIVE_3/MOSI: U5.15 (SDI_CFG1); also elsewhere on the board
/DRIVE_3/REFL_STEP: U5.17 (REFL_STEP); also elsewhere on the board
/DRIVE_3/REFR_DIR: U5.18 (REFR_DIR); also elsewhere on the board
/DRIVE_3/SCK: U5.14 (SCK_CFG2); also elsewhere on the board
/DRIVE_3/SRAH: U5.8 (SRAH); also elsewhere on the board
/DRIVE_3/SRAL: U5.7 (SRAL); also elsewhere on the board
/DRIVE_3/SRBH: U5.9 (SRBH); also elsewhere on the board
/DRIVE_3/SRBL: U5.10 (SRBL); also elsewhere on the board
/DRIVE_3/VCC_IO: C50.1, CR19.2, R124.2, R126.2, U5.20 (VCC_IO); also elsewhere on the board
/DRIVE_3/VM: C54.1, C55.1, C56.1, C57.1, C58.1, C59.1, CR19.1, U5.4 (VSA), U5.33 (VS); also elsewhere on the board
/DRIVE_3/~DRV_ENN: U5.28 (DRV_ENN); also elsewhere on the board
/DRIVE_4/BMA1: U6.40 (BMA1); also elsewhere on the board
/DRIVE_4/BMA2: U6.37 (BMA2); also elsewhere on the board
/DRIVE_4/BMB1: U6.48 (BMB1); also elsewhere on the board
/DRIVE_4/BMB2: U6.45 (BMB2); also elsewhere on the board
/DRIVE_4/CA1: U6.42 (CA1); also elsewhere on the board
/DRIVE_4/CA2: U6.35 (CA2); also elsewhere on the board
/DRIVE_4/CB1: U6.2 (CB1); also elsewhere on the board
/DRIVE_4/CB2: U6.43 (CB2); also elsewhere on the board
/DRIVE_4/CLK16: U6.12 (CLK); also elsewhere on the board
/DRIVE_4/CS: U6.13 (CSN_CFG3); also elsewhere on the board
/DRIVE_4/DIAG0: U6.26 (DIAG0_SWN); also elsewhere on the board
/DRIVE_4/DIAG1: U6.27 (DIAG1_SWP); also elsewhere on the board
/DRIVE_4/ENC_A: U6.24 (ENCA_DCIN_CFG5); also elsewhere on the board
/DRIVE_4/ENC_B: U6.23 (ENCB_DCEN_CFG4); also elsewhere on the board
/DRIVE_4/ENC_N: U6.25 (ENCN_DCO_CFG6); also elsewhere on the board
/DRIVE_4/HA1: U6.41 (HA1); also elsewhere on the board
/DRIVE_4/HA2: U6.36 (HA2); also elsewhere on the board
/DRIVE_4/HB1: U6.1 (HB1); also elsewhere on the board
/DRIVE_4/HB2: U6.44 (HB2); also elsewhere on the board
/DRIVE_4/LA1: U6.39 (LA1); also elsewhere on the board
/DRIVE_4/LA2: U6.38 (LA2); also elsewhere on the board
/DRIVE_4/LB1: U6.47 (LB1); also elsewhere on the board
/DRIVE_4/LB2: U6.46 (LB2); also elsewhere on the board
/DRIVE_4/MISO: U6.16 (SDO_CFG0); also elsewhere on the board
/DRIVE_4/MOSI: U6.15 (SDI_CFG1); also elsewhere on the board
/DRIVE_4/REFL_STEP: U6.17 (REFL_STEP); also elsewhere on the board
/DRIVE_4/REFR_DIR: U6.18 (REFR_DIR); also elsewhere on the board
/DRIVE_4/SCK: U6.14 (SCK_CFG2); also elsewhere on the board
/DRIVE_4/SRAH: U6.8 (SRAH); also elsewhere on the board
/DRIVE_4/SRAL: U6.7 (SRAL); also elsewhere on the board
/DRIVE_4/SRBH: U6.9 (SRBH); also elsewhere on the board
/DRIVE_4/SRBL: U6.10 (SRBL); also elsewhere on the board
/DRIVE_4/VCC_IO: C67.1, CR28.2, R143.2, R145.2, U6.20 (VCC_IO); also elsewhere on the board
/DRIVE_4/VM: C71.1, C72.1, C73.1, C74.1, C75.1, C76.1, CR28.1, U6.4 (VSA), U6.33 (VS); also elsewhere on the board
/DRIVE_4/~DRV_ENN: U6.28 (DRV_ENN); also elsewhere on the board
/DRIVE_5/BMA1: U7.40 (BMA1); also elsewhere on the board
/DRIVE_5/BMA2: U7.37 (BMA2); also elsewhere on the board
/DRIVE_5/BMB1: U7.48 (BMB1); also elsewhere on the board
/DRIVE_5/BMB2: U7.45 (BMB2); also elsewhere on the board
/DRIVE_5/CA1: U7.42 (CA1); also elsewhere on the board
/DRIVE_5/CA2: U7.35 (CA2); also elsewhere on the board
/DRIVE_5/CB1: U7.2 (CB1); also elsewhere on the board
/DRIVE_5/CB2: U7.43 (CB2); also elsewhere on the board
/DRIVE_5/CLK16: U7.12 (CLK); also elsewhere on the board
/DRIVE_5/CS: U7.13 (CSN_CFG3); also elsewhere on the board
/DRIVE_5/DIAG0: U7.26 (DIAG0_SWN); also elsewhere on the board
/DRIVE_5/DIAG1: U7.27 (DIAG1_SWP); also elsewhere on the board
/DRIVE_5/ENC_A: U7.24 (ENCA_DCIN_CFG5); also elsewhere on the board
/DRIVE_5/ENC_B: U7.23 (ENCB_DCEN_CFG4); also elsewhere on the board
/DRIVE_5/ENC_N: U7.25 (ENCN_DCO_CFG6); also elsewhere on the board
/DRIVE_5/HA1: U7.41 (HA1); also elsewhere on the board
/DRIVE_5/HA2: U7.36 (HA2); also elsewhere on the board
/DRIVE_5/HB1: U7.1 (HB1); also elsewhere on the board
/DRIVE_5/HB2: U7.44 (HB2); also elsewhere on the board
/DRIVE_5/LA1: U7.39 (LA1); also elsewhere on the board
/DRIVE_5/LA2: U7.38 (LA2); also elsewhere on the board
/DRIVE_5/LB1: U7.47 (LB1); also elsewhere on the board
/DRIVE_5/LB2: U7.46 (LB2); also elsewhere on the board
/DRIVE_5/MISO: U7.16 (SDO_CFG0); also elsewhere on the board
/DRIVE_5/MOSI: U7.15 (SDI_CFG1); also elsewhere on the board
/DRIVE_5/REFL_STEP: U7.17 (REFL_STEP); also elsewhere on the board
/DRIVE_5/REFR_DIR: U7.18 (REFR_DIR); also elsewhere on the board
/DRIVE_5/SCK: U7.14 (SCK_CFG2); also elsewhere on the board
/DRIVE_5/SRAH: U7.8 (SRAH); also elsewhere on the board
/DRIVE_5/SRAL: U7.7 (SRAL); also elsewhere on the board
/DRIVE_5/SRBH: U7.9 (SRBH); also elsewhere on the board
/DRIVE_5/SRBL: U7.10 (SRBL); also elsewhere on the board
/DRIVE_5/VCC_IO: C84.1, CR37.2, R3.2, R10.2, U7.20 (VCC_IO); also elsewhere on the board
/DRIVE_5/VM: C88.1, C89.1, C90.1, C91.1, C92.1, C93.1, CR37.1, U7.4 (VSA), U7.33 (VS); also elsewhere on the board
/DRIVE_5/~DRV_ENN: U7.28 (DRV_ENN); also elsewhere on the board
GND: C33.2, C34.1, C35.1, C36.2, C37.2, C38.2, C39.2, C40.2, C41.2, C50.2, C51.1, C52.1, C53.2, C54.2, C55.2, C56.2, C57.2, C58.2, C67.2, C68.1, C69.1, C70.2, C71.2, C72.2, C73.2, C74.2, C75.2, C84.2, C85.1, C86.1, C87.2, C88.2, C89.2, C90.2, C91.2, C92.2, R4.1, R11.1, R106.1, R108.1, R125.1, R127.1, R144.1, R146.1, U4.6 (GNDA), U4.11 (TST_MODE), U4.19 (GNDD), U4.30 (GNDD), U4.EPAD, U5.6 (GNDA), U5.11 (TST_MODE), U5.19 (GNDD), U5.30 (GNDD), U5.EPAD, U6.6 (GNDA), U6.11 (TST_MODE), U6.19 (GNDD), U6.30 (GNDD), U6.EPAD, U7.6 (GNDA), U7.11 (TST_MODE), U7.19 (GNDD), U7.30 (GNDD), U7.EPAD; also elsewhere on the board
unnamed: C34.2, R109.2, U4.5 (5VOUT)
unnamed: C35.2, U4.3 (12VOUT)
unnamed: C36.1, R109.1, U4.29 (VCC)
unnamed: C42.2, U4.34 (VCP)
unnamed: C43.1, U4.32 (CPI)
unnamed: C43.2, U4.31 (CPO)
unnamed: C51.2, R128.2, U5.5 (5VOUT)
unnamed: C52.2, U5.3 (12VOUT)
unnamed: C53.1, R128.1, U5.29 (VCC)
unnamed: C59.2, U5.34 (VCP)
unnamed: C60.1, U5.32 (CPI)
unnamed: C60.2, U5.31 (CPO)
unnamed: C68.2, R147.2, U6.5 (5VOUT)
unnamed: C69.2, U6.3 (12VOUT)
unnamed: C70.1, R147.1, U6.29 (VCC)
unnamed: C76.2, U6.34 (VCP)
unnamed: C77.1, U6.32 (CPI)
unnamed: C77.2, U6.31 (CPO)
unnamed: C85.2, R12.2, U7.5 (5VOUT)
unnamed: C86.2, U7.3 (12VOUT)
unnamed: C87.1, R12.1, U7.29 (VCC)
unnamed: C93.2, U7.34 (VCP)
unnamed: C94.1, U7.32 (CPI)
unnamed: C94.2, U7.31 (CPO)
unnamed: R3.1, R4.2, U7.22 (SPI_MODE)
unnamed: R10.1, R11.2, U7.21 (SD_MODE)
unnamed: R105.1, R106.2, U4.22 (SPI_MODE)
unnamed: R107.1, R108.2, U4.21 (SD_MODE)
unnamed: R124.1, R125.2, U5.22 (SPI_MODE)
unnamed: R126.1, R127.2, U5.21 (SD_MODE)
unnamed: R143.1, R144.2, U6.22 (SPI_MODE)
unnamed: R145.1, R146.2, U6.21 (SD_MODE)

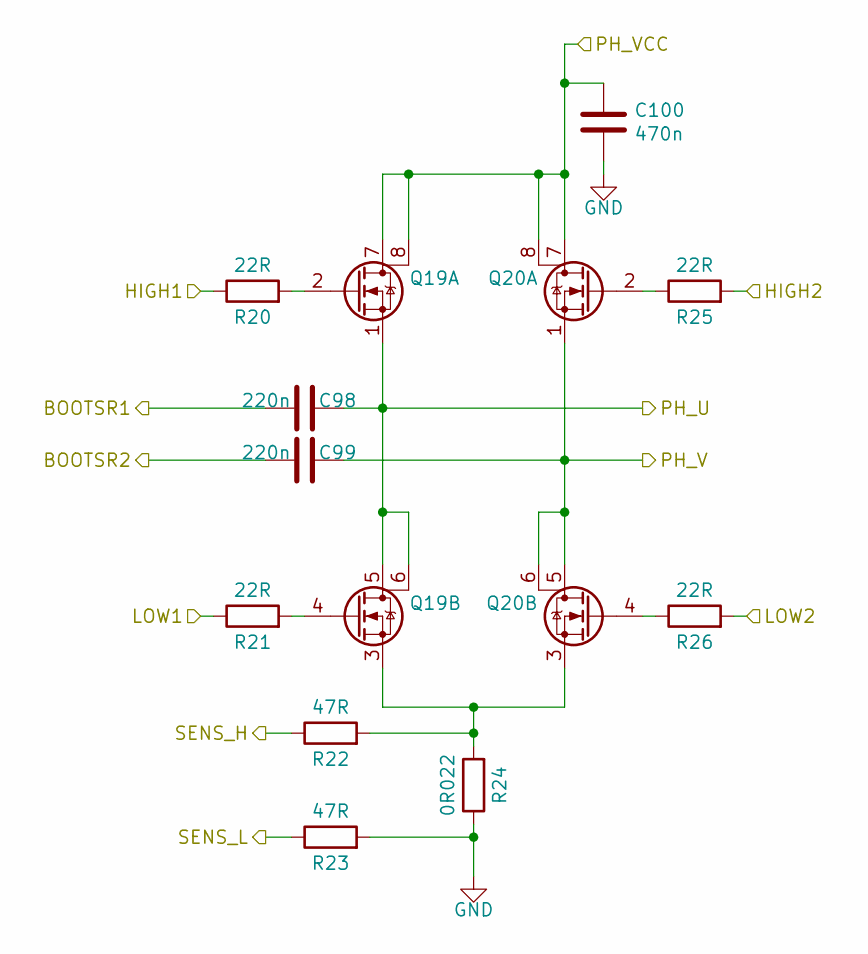
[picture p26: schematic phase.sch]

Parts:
C27, C28: 220n; C_0603_1608Metric_Pad1.05x0.95mm_HandSolder; MPN CL10F224ZB8NNNC
C29: 470n; C_0603_1608Metric_Pad1.05x0.95mm_HandSolder; MPN 885012106008
Q1, Q2: BUK9K45-100E,115; TRANS_BUK7K12-60EX; MPN BUK9K45-100E,115
R91, R92, R96, R97: 22R; R_0603_1608Metric_Pad1.05x0.95mm_HandSolder; MPN ERJ-3EKF22R0V
R93, R94: 47R; R_0603_1608Metric_Pad1.05x0.95mm_HandSolder; MPN CRGCQ0603F47R
R95: 0R022; WSH2818R0500FEA; MPN WSHM2818R0220FEA

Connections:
/DRIVE_1/BMA1: C27.1, Q1.1 (S), Q1.5 (D2), Q1.6 (D2); also elsewhere on the board
/DRIVE_1/BMA2: C28.1, Q2.1 (S), Q2.5 (D2), Q2.6 (D2); also elsewhere on the board
/DRIVE_1/CA1: C27.2; also elsewhere on the board
/DRIVE_1/CA2: C28.2; also elsewhere on the board
/DRIVE_1/HA1: R91.1; also elsewhere on the board
/DRIVE_1/HA2: R96.2; also elsewhere on the board
/DRIVE_1/LA1: R92.1; also elsewhere on the board
/DRIVE_1/LA2: R97.2; also elsewhere on the board
/DRIVE_1/SRAH: R93.1; also elsewhere on the board
/DRIVE_1/SRAL: R94.1; also elsewhere on the board
/DRIVE_1/VM: C29.1, Q1.7 (D2), Q1.8 (D2), Q2.7 (D2), Q2.8 (D2); also elsewhere on the board
GND: C29.2, R94.2, R95.1; also elsewhere on the board
unnamed: Q1.2 (G), R91.2
unnamed: Q1.3 (S), Q2.3 (S), R93.2, R95.2
unnamed: Q1.4 (G), R92.2
unnamed: Q2.2 (G), R96.1
unnamed: Q2.4 (G), R97.1

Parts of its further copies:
C30, C31, C44, C45, C47, C48, C61, C62, C64, C65, C78, C79, C81, C82, C95, C96, C98, C99: 220n; C_0603_1608Metric_Pad1.05x0.95mm_HandSolder; MPN CL10F224ZB8NNNC
C32, C46, C49, C63, C66, C80, C83, C97, C100: 470n; C_0603_1608Metric_Pad1.05x0.95mm_HandSolder; MPN 885012106008
Q3, Q4, Q5, Q6, Q7, Q8, Q9, Q10, Q11, Q12, Q13, Q14, Q15, Q16, Q17, Q18, Q19, Q20: BUK9K45-100E,115; TRANS_BUK7K12-60EX; MPN BUK9K45-100E,115
R13, R14, R18, R19, R20, R21, R25, R26, R98, R99, R103, R104, R110, R111, R115, R116, R117, R118, R122, R123, R129, R130, R134, R135, R136, R137, R141, R142, R148, R149, R153, R154, R155, R156, R160, R161: 22R; R_0603_1608Metric_Pad1.05x0.95mm_HandSolder; MPN ERJ-3EKF22R0V
R15, R16, R22, R23, R100, R101, R112, R113, R119, R120, R131, R132, R138, R139, R150, R151, R157, R158: 47R; R_0603_1608Metric_Pad1.05x0.95mm_HandSolder; MPN CRGCQ0603F47R
R17, R24, R102, R114, R121, R133, R140, R152, R159: 0R022; WSH2818R0500FEA; MPN WSHM2818R0220FEA

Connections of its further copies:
/DRIVE_1/BMB1: C30.1, Q3.1 (S), Q3.5 (D2), Q3.6 (D2); also elsewhere on the board
/DRIVE_1/BMB2: C31.1, Q4.1 (S), Q4.5 (D2), Q4.6 (D2); also elsewhere on the board
/DRIVE_1/CB1: C30.2; also elsewhere on the board
/DRIVE_1/CB2: C31.2; also elsewhere on the board
/DRIVE_1/HB1: R98.1; also elsewhere on the board
/DRIVE_1/HB2: R103.2; also elsewhere on the board
/DRIVE_1/LB1: R99.1; also elsewhere on the board
/DRIVE_1/LB2: R104.2; also elsewhere on the board
/DRIVE_1/SRBH: R100.1; also elsewhere on the board
/DRIVE_1/SRBL: R101.1; also elsewhere on the board
/DRIVE_1/VM: C32.1, Q3.7 (D2), Q3.8 (D2), Q4.7 (D2), Q4.8 (D2); also elsewhere on the board
/DRIVE_2/BMA1: C44.1, Q5.1 (S), Q5.5 (D2), Q5.6 (D2); also elsewhere on the board
/DRIVE_2/BMA2: C45.1, Q6.1 (S), Q6.5 (D2), Q6.6 (D2); also elsewhere on the board
/DRIVE_2/BMB1: C47.1, Q7.1 (S), Q7.5 (D2), Q7.6 (D2); also elsewhere on the board
/DRIVE_2/BMB2: C48.1, Q8.1 (S), Q8.5 (D2), Q8.6 (D2); also elsewhere on the board
/DRIVE_2/CA1: C44.2; also elsewhere on the board
/DRIVE_2/CA2: C45.2; also elsewhere on the board
/DRIVE_2/CB1: C47.2; also elsewhere on the board
/DRIVE_2/CB2: C48.2; also elsewhere on the board
/DRIVE_2/HA1: R110.1; also elsewhere on the board
/DRIVE_2/HA2: R115.2; also elsewhere on the board
/DRIVE_2/HB1: R117.1; also elsewhere on the board
/DRIVE_2/HB2: R122.2; also elsewhere on the board
/DRIVE_2/LA1: R111.1; also elsewhere on the board
/DRIVE_2/LA2: R116.2; also elsewhere on the board
/DRIVE_2/LB1: R118.1; also elsewhere on the board
/DRIVE_2/LB2: R123.2; also elsewhere on the board
/DRIVE_2/SRAH: R112.1; also elsewhere on the board
/DRIVE_2/SRAL: R113.1; also elsewhere on the board
/DRIVE_2/SRBH: R119.1; also elsewhere on the board
/DRIVE_2/SRBL: R120.1; also elsewhere on the board
/DRIVE_2/VM: C46.1, C49.1, Q5.7 (D2), Q5.8 (D2), Q6.7 (D2), Q6.8 (D2), Q7.7 (D2), Q7.8 (D2), Q8.7 (D2), Q8.8 (D2); also elsewhere on the board
/DRIVE_3/BMA1: C61.1, Q9.1 (S), Q9.5 (D2), Q9.6 (D2); also elsewhere on the board
/DRIVE_3/BMA2: C62.1, Q10.1 (S), Q10.5 (D2), Q10.6 (D2); also elsewhere on the board
/DRIVE_3/BMB1: C64.1, Q11.1 (S), Q11.5 (D2), Q11.6 (D2); also elsewhere on the board
/DRIVE_3/BMB2: C65.1, Q12.1 (S), Q12.5 (D2), Q12.6 (D2); also elsewhere on the board
/DRIVE_3/CA1: C61.2; also elsewhere on the board
/DRIVE_3/CA2: C62.2; also elsewhere on the board
/DRIVE_3/CB1: C64.2; also elsewhere on the board
/DRIVE_3/CB2: C65.2; also elsewhere on the board
/DRIVE_3/HA1: R129.1; also elsewhere on the board
/DRIVE_3/HA2: R134.2; also elsewhere on the board
/DRIVE_3/HB1: R136.1; also elsewhere on the board
/DRIVE_3/HB2: R141.2; also elsewhere on the board
/DRIVE_3/LA1: R130.1; also elsewhere on the board
/DRIVE_3/LA2: R135.2; also elsewhere on the board
/DRIVE_3/LB1: R137.1; also elsewhere on the board
/DRIVE_3/LB2: R142.2; also elsewhere on the board
/DRIVE_3/SRAH: R131.1; also elsewhere on the board
/DRIVE_3/SRAL: R132.1; also elsewhere on the board
/DRIVE_3/SRBH: R138.1; also elsewhere on the board
/DRIVE_3/SRBL: R139.1; also elsewhere on the board
/DRIVE_3/VM: C63.1, C66.1, Q9.7 (D2), Q9.8 (D2), Q10.7 (D2), Q10.8 (D2), Q11.7 (D2), Q11.8 (D2), Q12.7 (D2), Q12.8 (D2); also elsewhere on the board
/DRIVE_4/BMA1: C78.1, Q13.1 (S), Q13.5 (D2), Q13.6 (D2); also elsewhere on the board
/DRIVE_4/BMA2: C79.1, Q14.1 (S), Q14.5 (D2), Q14.6 (D2); also elsewhere on the board
/DRIVE_4/BMB1: C81.1, Q15.1 (S), Q15.5 (D2), Q15.6 (D2); also elsewhere on the board
/DRIVE_4/BMB2: C82.1, Q16.1 (S), Q16.5 (D2), Q16.6 (D2); also elsewhere on the board
/DRIVE_4/CA1: C78.2; also elsewhere on the board
/DRIVE_4/CA2: C79.2; also elsewhere on the board
/DRIVE_4/CB1: C81.2; also elsewhere on the board
/DRIVE_4/CB2: C82.2; also elsewhere on the board
/DRIVE_4/HA1: R148.1; also elsewhere on the board
/DRIVE_4/HA2: R153.2; also elsewhere on the board
/DRIVE_4/HB1: R155.1; also elsewhere on the board
/DRIVE_4/HB2: R160.2; also elsewhere on the board
/DRIVE_4/LA1: R149.1; also elsewhere on the board
/DRIVE_4/LA2: R154.2; also elsewhere on the board
/DRIVE_4/LB1: R156.1; also elsewhere on the board
/DRIVE_4/LB2: R161.2; also elsewhere on the board
/DRIVE_4/SRAH: R150.1; also elsewhere on the board
/DRIVE_4/SRAL: R151.1; also elsewhere on the board
/DRIVE_4/SRBH: R157.1; also elsewhere on the board
/DRIVE_4/SRBL: R158.1; also elsewhere on the board
/DRIVE_4/VM: C80.1, C83.1, Q13.7 (D2), Q13.8 (D2), Q14.7 (D2), Q14.8 (D2), Q15.7 (D2), Q15.8 (D2), Q16.7 (D2), Q16.8 (D2); also elsewhere on the board
/DRIVE_5/BMA1: C95.1, Q17.1 (S), Q17.5 (D2), Q17.6 (D2); also elsewhere on the board
/DRIVE_5/BMA2: C96.1, Q18.1 (S), Q18.5 (D2), Q18.6 (D2); also elsewhere on the board
/DRIVE_5/BMB1: C98.1, Q19.1 (S), Q19.5 (D2), Q19.6 (D2); also elsewhere on the board
/DRIVE_5/BMB2: C99.1, Q20.1 (S), Q20.5 (D2), Q20.6 (D2); also elsewhere on the board
/DRIVE_5/CA1: C95.2; also elsewhere on the board
/DRIVE_5/CA2: C96.2; also elsewhere on the board
/DRIVE_5/CB1: C98.2; also elsewhere on the board
/DRIVE_5/CB2: C99.2; also elsewhere on the board
/DRIVE_5/HA1: R13.1; also elsewhere on the board
/DRIVE_5/HA2: R18.2; also elsewhere on the board
/DRIVE_5/HB1: R20.1; also elsewhere on the board
/DRIVE_5/HB2: R25.2; also elsewhere on the board
/DRIVE_5/LA1: R14.1; also elsewhere on the board
/DRIVE_5/LA2: R19.2; also elsewhere on the board
/DRIVE_5/LB1: R21.1; also elsewhere on the board
/DRIVE_5/LB2: R26.2; also elsewhere on the board
/DRIVE_5/SRAH: R15.1; also elsewhere on the board
/DRIVE_5/SRAL: R16.1; also elsewhere on the board
/DRIVE_5/SRBH: R22.1; also elsewhere on the board
/DRIVE_5/SRBL: R23.1; also elsewhere on the board
/DRIVE_5/VM: C97.1, C100.1, Q17.7 (D2), Q17.8 (D2), Q18.7 (D2), Q18.8 (D2), Q19.7 (D2), Q19.8 (D2), Q20.7 (D2), Q20.8 (D2); also elsewhere on the board
GND: C32.2, C46.2, C49.2, C63.2, C66.2, C80.2, C83.2, C97.2, C100.2, R16.2, R17.1, R23.2, R24.1, R101.2, R102.1, R113.2, R114.1, R120.2, R121.1, R132.2, R133.1, R139.2, R140.1, R151.2, R152.1, R158.2, R159.1; also elsewhere on the board
unnamed: Q3.2 (G), R98.2
unnamed: Q3.3 (S), Q4.3 (S), R100.2, R102.2
unnamed: Q3.4 (G), R99.2
unnamed: Q4.2 (G), R103.1
unnamed: Q4.4 (G), R104.1
unnamed: Q5.2 (G), R110.2
unnamed: Q5.3 (S), Q6.3 (S), R112.2, R114.2
unnamed: Q5.4 (G), R111.2
unnamed: Q6.2 (G), R115.1
unnamed: Q6.4 (G), R116.1
unnamed: Q7.2 (G), R117.2
unnamed: Q7.3 (S), Q8.3 (S), R119.2, R121.2
unnamed: Q7.4 (G), R118.2
unnamed: Q8.2 (G), R122.1
unnamed: Q8.4 (G), R123.1
unnamed: Q9.2 (G), R129.2
unnamed: Q9.4 (G), R130.2
unnamed: Q10.2 (G), R134.1
unnamed: Q9.3 (S), Q10.3 (S), R131.2, R133.2
unnamed: Q10.4 (G), R135.1
unnamed: Q11.2 (G), R136.2
unnamed: Q11.3 (S), Q12.3 (S), R138.2, R140.2
unnamed: Q11.4 (G), R137.2
unnamed: Q12.2 (G), R141.1
unnamed: Q12.4 (G), R142.1
unnamed: Q13.2 (G), R148.2
unnamed: Q13.3 (S), Q14.3 (S), R150.2, R152.2
unnamed: Q13.4 (G), R149.2
unnamed: Q14.2 (G), R153.1
unnamed: Q14.4 (G), R154.1
unnamed: Q15.2 (G), R155.2
unnamed: Q15.3 (S), Q16.3 (S), R157.2, R159.2
unnamed: Q15.4 (G), R156.2
unnamed: Q16.2 (G), R160.1
unnamed: Q16.4 (G), R161.1
unnamed: Q17.2 (G), R13.2
unnamed: Q17.3 (S), Q18.3 (S), R15.2, R17.2
unnamed: Q17.4 (G), R14.2
unnamed: Q18.2 (G), R18.1
unnamed: Q18.4 (G), R19.1
unnamed: Q19.2 (G), R20.2
unnamed: Q19.3 (S), Q20.3 (S), R22.2, R24.2
unnamed: Q19.4 (G), R21.2
unnamed: Q20.2 (G), R25.1
unnamed: Q20.4 (G), R26.1

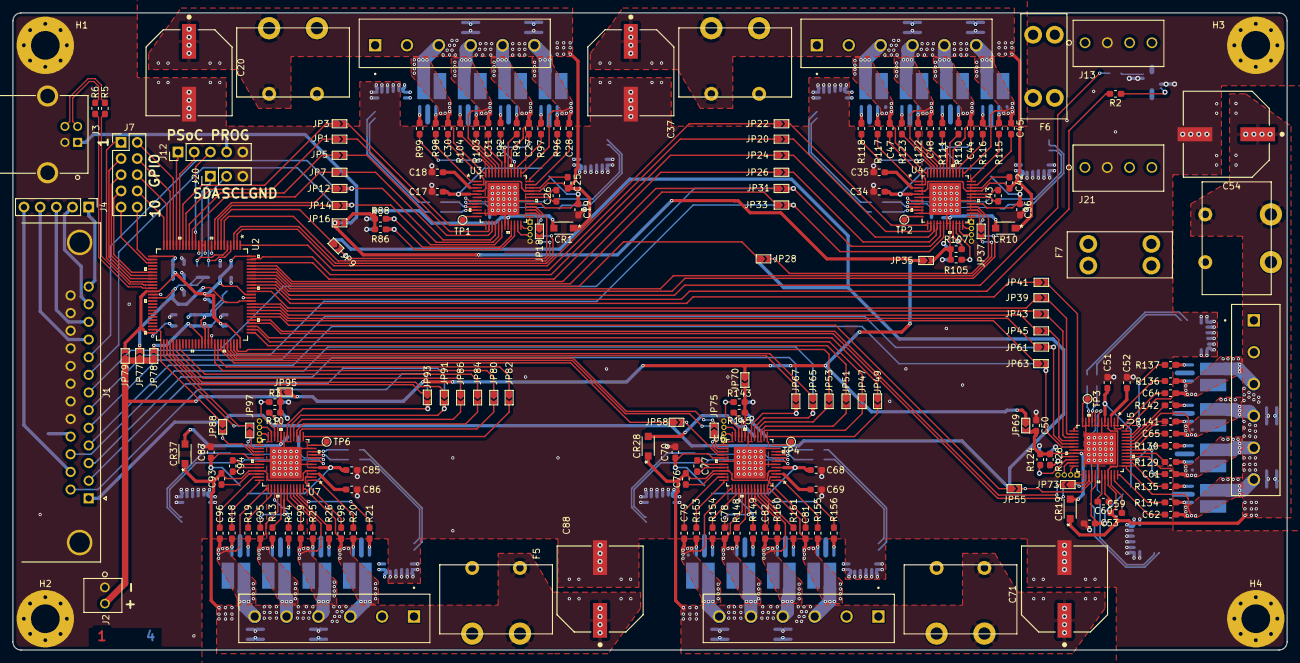
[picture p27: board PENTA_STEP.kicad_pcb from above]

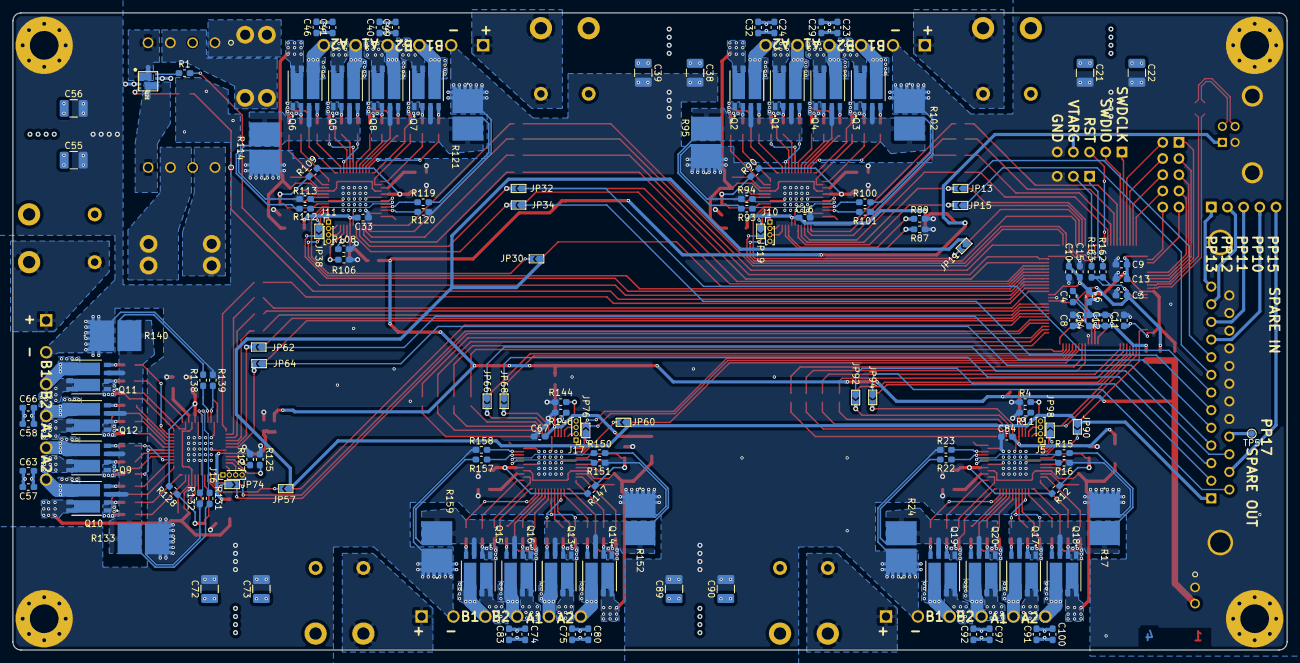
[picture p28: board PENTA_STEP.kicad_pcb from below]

Board: 4 copper layers, 200.0 x 100.0 mm, 333 parts (140 on the bottom side), 367 nets.

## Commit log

2019-12-26 rough BOM, have primary components.
    [01005R.stp, 0201R.stp, 0402R.stp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]
2019-12-27 began H-bridge stage
    [14S1-L.step, 14S1-M.step, 14S1.step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]
2019-12-28 finished h bridges, converted to hierarchical layout
    [QUAD_STEP.sch, drive.sch, phase.sch]
2019-12-30 added more components, fleshed out DB-25 interface, added PSoC
    [QUAD_STEP.sch, drive.sch, phase.sch]
2020-01-05 many changes, fixed issue with hierarchical(sp?) pins
    [1935161--3DModel-STEP-56544.STEP, CUI_DEVICES_TB002-500-06BE.step]
2020-01-09 beginning layout
    [2019-12-25T201518.xlsx, CY8CKIT-059_PCBA_BOM.xlsx, EEV-EB2D101M--3DModel-STEP-56544.STEP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]
2020-01-10 complebegan adding 3D files
    [CUI_DEVICES_UJ2-BH-W1-TH.step, QUAD_STEP.kicad_pcb, QUAD_STEP.sch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]
2020-01-10 added some 3D files, converted to personal computer paths
    [QUAD_STEP.kicad_pcb]
2020-01-12 changed scope to 5 axis, preliminary completion of component positioning
    [EDH108M016A9RAA.step, QUAD_STEP.kicad_pcb, QUAD_STEP.sch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]
2020-01-13 3D links buggered, tinkered with alternate placement of FETs
    [QUAD_STEP.kicad_pcb]
2020-01-19 corrected symbol and footprint paths
    [01005R.stp, 0201R.stp, 0402R.stp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]
2020-01-19 progressing on layout
    [PENTA_STEP.kicad_pcb]
2020-01-21 V1 layout nearing completion
    [PENTA_STEP.kicad_pcb, PENTA_STEP.sch, drive.sch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]
2020-01-22 Added two FET-controlled outputs to the board
    [PENTA_STEP.kicad_pcb, PENTA_STEP.sch, drive.sch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]
2020-01-27 majority routed, eliminated ATTINY coprocessor
    [DIODE_SOD123LF_2P9X1P8-L.step, DIODE_SOD123LF_2P9X1P8-M.step, DIODE_SOD123LF_2P9X1P8.step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]
2020-01-29 completed preliminary routing, still need plane touchup
    [PENTA_STEP.kicad_pcb, PENTA_STEP.sch, drive.sch]
2020-02-02 finished layout, added top and bottom layer ground pours, added fuses for FET outputs
    [PENTA_STEP.sch, keystone-PN3568-10_THT.STEP]
2020-02-02 finished layout, added top and bottom layer ground pours, added fuses for FET outputs, but forgot to save ;)
    [PENTA_STEP.kicad_pcb]
2020-02-25 finalized BOM, found TMC5160-TA being replaced by TMC5160A-TA
    [FINAL_BOM.ods, PENTA_STEP.kicad_pcb, PENTA_STEP.sch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]

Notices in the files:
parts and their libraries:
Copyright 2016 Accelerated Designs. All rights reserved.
